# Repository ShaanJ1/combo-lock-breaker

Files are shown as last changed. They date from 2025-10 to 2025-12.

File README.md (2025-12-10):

# Combo Lock Breaker
This device can cycle through every possible combination on your lock until it finds the correct code, which is then displayed on an LCD screen. In the future this device will also be able to use Samy Kamkar's method to crack locks even faster.
### Highlights
- Fast and Accurate
- Cracks any combination lock in under ____ minutes
- LCD displays the current status, progress, and more
- Quiet & Efficient
### Showcase
*Coming soon...*
### Bill of Materials (BOM)

| **Item Name** | **URL** | **Price** | **Quantity** | **Per Package** | **Use** |
|---|---|---|---|---|---|
| Power Supply Cable | [AliExpress](https://www.aliexpress.com/item/1005007332397741.html) | $16.96 | 1 | 1 | Power |
| Nema 17 Motor | [AliExpress](https://www.aliexpress.com/item/32572890101.html?spm=a2g0o.cart.0.0.66ba38daMIFTUY&mp=1) | $23.98 | 1 | 1 | Dial turning mechanism |
| TMC2209 | [AliExpress](https://www.aliexpress.com/item/33028050145.html) | $7.49 | 1 | 3 | Motor driver |
| Analog Feedback Servo | [AliExpress](https://www.aliexpress.com/item/1005007407524023.html) | $14.81 | 1 | 1 | Shackle opening mechanism  |
| 4x4 Matrix Keypad | [AliExpress](https://www.aliexpress.com/item/1005007182495122.html?spm=a2g0o.cart.0.0.56ba38da4Y49U1&mp=1) | $2.00 | 1 | 1 | User input |
| LCD1602 I2C | [AliExpress](https://www.aliexpress.com/item/1005006151355330.html?spm=a2g0o.cart.0.0.56ba38da4Y49U1&mp=1) | $4.13 | 1 | 1 | Displays program output |
| M3 6mm Screws | [AliExpress](https://www.aliexpress.com/item/1005007264845313.html) | $2.96 | 1 | 50 | Mounting screws |
| M2.5 10mm Screws | [AliExpress](https://www.aliexpress.com/item/1005007264845313.html) | $2.96 | 1 | 50 | Mounting screws |
| M2.5 5mm Screws | [AliExpress](https://www.aliexpress.com/item/1005007264845313.html) | $2.96 | 1 | 50 | Mounting screws |
| M2 5mm Screws | [AliExpress](https://www.aliexpress.com/item/1005007264845313.html) | $2.96 | 1 | 50 | Mounting screws |
| PCBA | [JLCPCB](https://jlcpcb.com) | $73.61 | 1 | 5 PCB, 2 PCBA | Main controller |
| 1x3 PinHeader | [DigiKey](https://www.digikey.ca/en/products/detail/w%C3%BCrth-elektronik/61300311121/4846825) | $0.18 | 1 | 1 | Debug connector |
| 1x4 PinHeader | [DigiKey](https://www.digikey.ca/en/products/detail/w%C3%BCrth-elektronik/61300411121/4846827) | $0.50 | 3 | 1 | LCD & servo connectors |
| 1x8 PinHeader | [DigiKey](https://www.digikey.ca/en/products/detail/w%C3%BCrth-elektronik/61300811121/4846839) | $0.54 | 1 | 1 | Keypad connector |
| Barrel Jack | [DigiKey](https://www.digikey.ca/en/products/detail/switchcraft-inc/RAPC712BKZ/9997462) | $4.41 | 1 | 1 | Power connector |

**Total (CAD):** $165.79

**Total (USD):** $117.67

### Images
Schematic




PCB


Main Assembly



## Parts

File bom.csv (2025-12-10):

Bill of Materials
Item Name: | URL: | Price: | Quantity: | Per package | Use:
Power Supply Cable | https://www.aliexpress.com/item/1005007332397741.html | $16.96 | 1 | 1 | Power
Nema 17 Motor | https://www.aliexpress.com/item/32572890101.html?spm=a2g0o.cart.0.0.66ba38daMIFTUY&mp=1 | $23.98 | 1 | 1 | Dial turning mechanism
TMC2209 | https://www.aliexpress.com/item/33028050145.html | $7.49 | 1 | 3 | Motor Driver
Analog Feedback Servo | https://www.aliexpress.com/item/1005007407524023.html | $14.81 | 1 | 1 | Shackle opening mechanism
4x4 Matrix Keypad | https://www.aliexpress.com/item/1005007182495122.html?spm=a2g0o.cart.0.0.56ba38da4Y49U1&mp=1 | $2.00 | 1 | 1 | User input
LCD1602 I2C | https://www.aliexpress.com/item/1005006151355330.html?mp=1 | $4.13 | 1 | 1 | Displays program output
M3 6mm Screws | https://www.aliexpress.com/item/1005007264845313.html?mp=1 | $2.96 | 1 | 50 | Mounting screws
M2.5 10mm Screws | https://www.aliexpress.com/item/1005007264845313.html?mp=1 | $2.96 | 1 | 50 | Mounting screws
M2.5 5mm Screws | https://www.aliexpress.com/item/1005007264845313.html?mp=1 | $2.96 | 1 | 50 | Mounting Screws
M2 5mm Screws | https://www.aliexpress.com/item/1005007264845313.html?mp=1 | $2.96 | 1 | 50 | Mounting Screws
PCBA | https://jlcpcb.com | $73.61 | 1 | 5 PCB, 2 PCBA | Main Controller
1x3 PinHeader | https://www.digikey.ca/en/products/detail/w%C3%BCrth-elektronik/61300311121/4846825 | $0.18 | 1 | 1 | Debug Connector
1x4 PinHeader | https://www.digikey.ca/en/products/detail/w%C3%BCrth-elektronik/61300411121/4846827 | $0.50 | 3 | 1 | LCD, Motor, & Servo Connectors
1x8 PinHeader | https://www.digikey.ca/en/products/detail/w%C3%BCrth-elektronik/61300811121/4846839 | $0.54 | 1 | 1 | Keypad Connectors
Barrel Jack | https://www.digikey.ca/en/products/detail/switchcraft-inc/RAPC712BKZ/9997462 | $4.41 | 1 | 1 | Power Connector
 | Total (CAD): | $160.45
 | Total: (USD): | $114.35

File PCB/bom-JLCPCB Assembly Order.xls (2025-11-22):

JLCPCB BOM Tool - BOM Matching
BOM name：bom-JLCPCB Assembly Order.xlsx |  |  | Download Time：2025-11-21 13:03:07 |  |  |  | * Our matching results are updated in real-time, but stock and prices may change. If it's been over 24 hours, please re-match before placing your order.
PCB Assembled Qty：5 |  |  | Est. Total Price：9.0908
Your BOM |  |  |  |  | Matched Parts |  |  |  |  |  |  | Order Information
Top Designator | Bottom Designator | Comment | Footprint | JLCPCB Part # | Matches | Part # | Manufacturer | Footprint | Description | Category | Warning | JLCPCB Part # | Product link | Lib Type | Qty | Source | Total Price ($)
C1,C2 |  | 10uF | 0603 |  | Select by System | CL10A106KP8NNNC | Samsung Electro-Mechanics | 0603 | 10V 10uF X5R ±10% 0603 Multilayer Ceramic Capacitors MLCC - SMD/SMT ROHS | Multilayer Ceramic Capacitors MLCC - SMD/SMT |  | C19702 | https://jlcpcb.com/partdetail/20411-CL10A106KP8NNNC/C19702 | Basic | 4 | 4 JLCPCB | 0.0224
C4 |  | 22uF | 1206 |  | Select by System | CL31A226KAHNNNE | Samsung Electro-Mechanics | 1206 | 22uF 25V X5R ±10% 1206 Multilayer Ceramic Capacitors MLCC - SMD/SMT ROHS | Multilayer Ceramic Capacitors MLCC - SMD/SMT |  | C12891 | https://jlcpcb.com/partdetail/13537-CL31A226KAHNNNE/C12891 | Basic | 2 | 2 JLCPCB | 0.0796
C6 |  | 100nF | 0805 |  | Select by System | CC0805KRX7R9BB104 | YAGEO | 0805 | 100nF 50V X7R ±10% 0805 Multilayer Ceramic Capacitors MLCC - SMD/SMT ROHS | Multilayer Ceramic Capacitors MLCC - SMD/SMT |  | C49678 | https://jlcpcb.com/partdetail/YAGEO-CC0805KRX7R9BB104/C49678 | Basic | 2 | 2 JLCPCB | 0.0086
C7 |  | 75pF | 0402 |  | Select by System | CC0402JRNPO9BN750 | YAGEO | 0402 | 50V 75pF NP0 ±5% 0402 Multilayer Ceramic Capacitors MLCC - SMD/SMT ROHS | Multilayer Ceramic Capacitors MLCC - SMD/SMT |  | C107010 | https://jlcpcb.com/partdetail/YAGEO-CC0402JRNPO9BN750/C107010 | Extended | 20 | 20 JLCPCB | 0.022
C10,C11,C12,C13,C14,C15,C17,C20,C24,C29,C8,C9 |  | 0.1uF | 0402 |  | Select by Customer | CL05B104KO5NNNC | Samsung Electro-Mechanics | 0402 | 100nF 16V X7R ±10% 0402 Multilayer Ceramic Capacitors MLCC - SMD/SMT ROHS | Multilayer Ceramic Capacitors MLCC - SMD/SMT | 1.The comment (CL05B104KO5NNNC) of this part does not match the one (0.1uF) provided in your BOM. Please confirm; | C1525 | https://jlcpcb.com/partdetail/1877-CL05B104KO5NNNC/C1525 | Basic | 24 | 24 JLCPCB | 0.0288
C16,C3 |  | 1uF | 0402 |  | Select by System | CL05A105KA5NQNC | Samsung Electro-Mechanics | 0402 | 1uF 25V X5R ±10% 0402 Multilayer Ceramic Capacitors MLCC - SMD/SMT ROHS | Multilayer Ceramic Capacitors MLCC - SMD/SMT |  | C52923 | https://jlcpcb.com/partdetail/53938-CL05A105KA5NQNC/C52923 | Basic | 4 | 4 JLCPCB | 0.0116
C18,C19 |  | 33pF | 0402 |  | Select by System | 0402CG330J500NT | FH (Guangdong Fenghua Advanced Tech) | 0402 | 33pF 50V C0G ±5% 0402 Multilayer Ceramic Capacitors MLCC - SMD/SMT ROHS | Multilayer Ceramic Capacitors MLCC - SMD/SMT |  | C1562 | https://jlcpcb.com/partdetail/1914-0402CG330J500NT/C1562 | Basic | 4 | 4 JLCPCB | 0.004
C21 |  | 47uF | 0805 |  | Select by System | CL21A476MQYNNNE | Samsung Electro-Mechanics | 0805 | 47uF 6.3V X5R ±20% 0805 Multilayer Ceramic Capacitors MLCC - SMD/SMT ROHS | Multilayer Ceramic Capacitors MLCC - SMD/SMT |  | C16780 | https://jlcpcb.com/partdetail/17464-CL21A476MQYNNNE/C16780 | Basic | 2 | 2 JLCPCB | 0.051
C22 |  | 47uF | 1206 |  | Select by System | CL31A476MPHNNNE | Samsung Electro-Mechanics | 1206 | 10V 47uF X5R ±20% 1206 Multilayer Ceramic Capacitors MLCC - SMD/SMT ROHS | Multilayer Ceramic Capacitors MLCC - SMD/SMT |  | C96123 | https://jlcpcb.com/partdetail/97327-CL31A476MPHNNNE/C96123 | Basic | 2 | 2 JLCPCB | 0.1362
C25,C5 |  | 100uF | CP_Elec_6.3x7.7 |  | Select by Customer | RVT1V101M0607 | Honor Elec | SMD,D6.3xL7.7mm | -55℃~+105℃ 100uF 2000hrs@105℃ 35V 6.3mm 7.7mm ±20% SMD,D6.3xL7.7mm Aluminum Electrolytic Capacitors - SMD ROHS | Aluminum Electrolytic Capacitors - SMD |  | C3339 | https://jlcpcb.com/partdetail/HonorElec-RVT1V101M0607/C3339 | Extended | 6 | 6 JLCPCB | 0.2118
D1,D2,D3,D4 |  | SS34 | D_SMA |  | Select by System | SS34 | MDD(Microdiode Semiconductor) | SMA(DO-214AC) | -55℃~+125℃ 3A 40V 500uA@40V 550mV@3A Independent SMA(DO-214AC) Schottky Diodes ROHS | Schottky Diodes |  | C8678 | https://jlcpcb.com/partdetail/MDD_Microdiode_Semiconductor-SS34/C8678 | Basic | 8 | 8 JLCPCB | 0.2208
J2 |  | USB_C_Receptacle_USB2.0_14P | USB_C_Receptacle_HRO_TYPE-C-31-M-12 |  | Select by Customer | TYPE-C-31-M-12 | Korean Hroparts Elec | SMD | 1 16P 5A Female Type-C SMD USB Connectors ROHS | USB Connectors |  | C165948 | https://jlcpcb.com/partdetail/Korean_HropartsElec-TYPE_C_31_M12/C165948 | Extended | 2 | 2 JLCPCB | 0.3388
L1 |  | 4.7uH | L_7.3x7.3_H3.5 |  | Select by System | SLH0704S4R7MTT | Sunltech Tech | SMD,7.3x7.3mm | 3.5A 39mΩ 4.7uH Magnetic Shielded Inductor ±20% SMD,7.3x7.3mm Power Inductors ROHS | Power Inductors |  | C182156 | https://jlcpcb.com/partdetail/SunltechTech-SLH0704S4R7MTT/C182156 | Extended | 3 | 3 JLCPCB | 0.3732
R1,R2 |  | 5.1K | 0402 |  | Select by Customer | 0402WGF5101TCE | UNI-ROYAL(Uniroyal Elec) | 0402 | -55℃~+155℃ 5.1kΩ 50V 62.5mW Thick Film Resistor ±1% ±100ppm/℃ 0402 Chip Resistor - Surface Mount ROHS | Chip Resistor - Surface Mount | 1.The comment (0402WGF5101TCE) of this part does not match the one (5.1K) provided in your BOM. Please confirm; | C25905 | https://jlcpcb.com/partdetail/26648-0402WGF5101TCE/C25905 | Basic | 4 | 4 JLCPCB | 0.002
R3,R4 |  | 27 | 0402 |  | Select by Customer | 0402WGF270JTCE | UNI-ROYAL(Uniroyal Elec) | 0402 | -55℃~+155℃ 27Ω 50V 62.5mW Thick Film Resistor ±1% ±100ppm/℃ 0402 Chip Resistor - Surface Mount ROHS | Chip Resistor - Surface Mount | 1.The comment (0402WGF270JTCE) of this part does not match the one (27) provided in your BOM. Please confirm; | C25100 | https://jlcpcb.com/partdetail/25843-0402WGF270JTCE/C25100 | Extended | 20 | 20 JLCPCB | 0.012
R5,R7 |  | 1K | 0402 |  | Select by Customer | 0402WGF1001TCE | UNI-ROYAL(Uniroyal Elec) | 0402 | -55℃~+155℃ 1kΩ 50V 62.5mW Thick Film Resistor ±1% ±100ppm/℃ 0402 Chip Resistor - Surface Mount ROHS | Chip Resistor - Surface Mount | 1.The comment (0402WGF1001TCE) of this part does not match the one (1K) provided in your BOM. Please confirm; | C11702 | https://jlcpcb.com/partdetail/12256-0402WGF1001TCE/C11702 | Basic | 4 | 4 JLCPCB | 0.0024
R6 |  | 10K | 0402 |  | Select by Customer | 0402WGF1002TCE | UNI-ROYAL(Uniroyal Elec) | 0402 | -55℃~+155℃ 10kΩ 50V 62.5mW Thick Film Resistor ±1% ±100ppm/℃ 0402 Chip Resistor - Surface Mount ROHS | Chip Resistor - Surface Mount | 1.The comment (0402WGF1002TCE) of this part does not match the one (10K) provided in your BOM. Please confirm; | C25744 | https://jlcpcb.com/partdetail/26487-0402WGF1002TCE/C25744 | Basic | 2 | 2 JLCPCB | 0.0012
R8 |  | 100K | 0603 |  | Select by Customer | 0603WAF1003T5E | UNI-ROYAL(Uniroyal Elec) | 0603 | -55℃~+155℃ 100kΩ 100mW 75V Thick Film Resistor ±1% ±100ppm/℃ 0603 Chip Resistor - Surface Mount ROHS | Chip Resistor - Surface Mount | 1.The comment (0603WAF1003T5E) of this part does not match the one (100K) provided in your BOM. Please confirm; | C25803 | https://jlcpcb.com/partdetail/26546-0603WAF1003T5E/C25803 | Basic | 2 | 2 JLCPCB | 0.002
R9 |  | 13.7K | 0603 |  | Select by Customer | 0603WAF1372T5E | UNI-ROYAL(Uniroyal Elec) | 0603 | -55℃~+155℃ 100mW 13.7kΩ 75V Thick Film Resistor ±1% ±100ppm/℃ 0603 Chip Resistor - Surface Mount ROHS | Chip Resistor - Surface Mount | 1.The comment (0603WAF1372T5E) of this part does not match the one (13.7K) provided in your BOM. Please confirm; | C22793 | https://jlcpcb.com/partdetail/23520-0603WAF1372T5E/C22793 | Extended | 20 | 20 JLCPCB | 0.022
R21,R22 |  | 4.7K | 0402 |  | Select by Customer | 0402WGF4701TCE | UNI-ROYAL(Uniroyal Elec) | 0402 | -55℃~+155℃ 4.7kΩ 50V 62.5mW Thick Film Resistor ±1% ±100ppm/℃ 0402 Chip Resistor - Surface Mount ROHS | Chip Resistor - Surface Mount | 1.The comment (0402WGF4701TCE) of this part does not match the one (4.7K) provided in your BOM. Please confirm; | C25900 | https://jlcpcb.com/partdetail/26643-0402WGF4701TCE/C25900 | Basic | 4 | 4 JLCPCB | 0.0024
SW1 |  | SW_Push | SW_Push_SPST_NO_Alps_SKRK |  | Select by Customer | TS-1088-AR02016 | XUNPU | SMD,4x3mm | -30℃~+80℃ 1.6N 100,000 Cycles 12V 2mm 3mm 4mm 50mA Black Round Button SMD(SMT) Tab SPST Surface Mount,Vertical Without Bracket SMD,4x3mm Tactile Switches ROHS | Tactile Switches |  | C720477 | https://jlcpcb.com/partdetail/XUNPU-TS_1088AR02016/C720477 | Basic | 2 | 2 JLCPCB | 0.085
U1 |  | MCP1700x-330xxTT | SOT-23 |  | Select by Customer | MCP1700T-3302E/TT | Microchip Tech | SOT-23 | -40℃~+125℃@(Tj) 1 1.6uA 178mV@(250mA) 250mA 3.3V 44dB@(100Hz) 6V Fixed Over Temperature Protection Positive SOT-23 Voltage Regulators - Linear, Low Drop Out (LDO) Regulators ROHS | Voltage Regulators - Linear, Low Drop Out (LDO) Regulators |  | C39051 | https://jlcpcb.com/partdetail/MicrochipTech-MCP1700T_3302ETT/C39051 | Extended | 5 | 5 JLCPCB | 1.9695
U2 |  | W25Q128JVS | SOIC-8_5.3x5.3mm_P1.27mm |  | Select by Customer | W25Q128JVSIQ | Winbond Elec | SOIC-8-208mil | -40℃~+85℃ 100,000 Cycles 120ms@(32KB) 128Mbit 133MHz 1uA 2.7V~3.6V 20 Years 3ms SPI SOIC-8-208mil NOR FLASH ROHS | NOR FLASH | 1.The comment (W25Q128JVSIQ) of this part does not match the one (W25Q128JVS) provided in your BOM. Please confirm; | C97521 | https://jlcpcb.com/partdetail/WinbondElec-W25Q128JVSIQ/C97521 | Basic | 2 | 2 JLCPCB | 2.667
U3 |  | RP2040 | QFN-56-1EP_7x7mm_P0.4mm_EP3.2x3.2mm |  | Select by Customer | RP2040 | Raspberry Pi | LQFN-56(7x7) | 12bit 133MHz 30 LQFN-56(7x7) Microcontrollers (MCU/MPU/SOC) ROHS | Microcontrollers (MCU/MPU/SOC) |  | C2040 | https://jlcpcb.com/partdetail/RaspberryPi-RP2040/C2040 | Extended | 2 | 2 JLCPCB | 1.833
U6 |  | TPS54302 | SOT-23-6 |  | Select by Customer | TPS54302DDCR | Texas Instruments | TSOT-23-6 | -40℃~+125℃@(TJ) 1 3A 4.5V~28V 400kHz 45uA Adjustable Buck Buck Built-In Yes TSOT-23-6 DC-DC Converters ROHS | DC-DC Converters | 1.The comment (TPS54302DDCR) of this part does not match the one (TPS54302) provided in your BOM. Please confirm; | C311983 | https://jlcpcb.com/partdetail/TexasInstruments-TPS54302DDCR/C311983 | Extended | 5 | 5 JLCPCB | 0.8545
Y1 |  | 12MHz | Crystal_SMD_3225-4Pin_3.2x2.5mm |  | Select by Customer | X322512MSB4SI | YXC Crystal Oscillators | SMD3225-4P | -40℃~+85℃ 12MHz 20pF Crystal Oscillator ±10ppm ±20ppm SMD3225-4P Crystals ROHS | Crystals |  | C9002 | https://jlcpcb.com/partdetail/YXC_CrystalOscillators-X322512MSB4SI/C9002 | Basic | 2 | 2 JLCPCB | 0.129
J1 |  | Barrel_Jack_MountingPin | BarrelJack_GCT_DCJ200-10-A_Horizontal |  | No matches | No Part Selected
J3 |  | Conn_01x04 | PinHeader_1x04_P2.54mm_Vertical |  | No matches | No Part Selected
J4 |  | TMC2209_Module_v1.3 | TMC2209 |  | No matches | No Part Selected
J5 |  | 4x4MatrixKeypad | PinHeader_1x08_P2.54mm_Vertical |  | No matches | No Part Selected
J6 |  | Conn_01x03 | PinHeader_1x03_P2.54mm_Vertical |  | No matches | No Part Selected
J8 |  | I2C_LCD_1602 | PinHeader_1x04_P2.54mm_Vertical |  | No matches | No Part Selected
J11 |  | Analog_Feedback_Servo | PinHeader_1x04_P2.54mm_Vertical |  | No matches | No Part Selected

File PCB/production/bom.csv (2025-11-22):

Designator | Footprint | Quantity | Value | LCSC Part #
C1, C2 | 0603 | 2 | 10uF
C10, C11, C12, C13, C14, C15, C17, C20, C24, C29, C8, C9 | 0402 | 12 | 0.1uF
C16, C3 | 0402 | 2 | 1uF
C18, C19 | 0402 | 2 | 33pF
C21 | 0805 | 1 | 47uF
C22 | 1206 | 1 | 47uF
C25, C5 | CP_Elec_6.3x7.7 | 2 | 100uF
C4 | 1206 | 1 | 22uF
C6 | 0805 | 1 | 100nF
C7 | 0402 | 1 | 75pF
D1, D2, D3, D4 | D_SMA | 4 | SS34
J1 | BarrelJack_GCT_DCJ200-10-A_Horizontal | 1 | Barrel_Jack_MountingPin
J11 | PinHeader_1x04_P2.54mm_Vertical | 1 | Analog_Feedback_Servo
J2 | USB_C_Receptacle_HRO_TYPE-C-31-M-12 | 1 | USB_C_Receptacle_USB2.0_14P
J3 | PinHeader_1x04_P2.54mm_Vertical | 1 | Conn_01x04
J4 | TMC2209 | 1 | TMC2209_Module_v1.3
J5 | PinHeader_1x08_P2.54mm_Vertical | 1 | 4x4 Matrix Keypad
J6 | PinHeader_1x03_P2.54mm_Vertical | 1 | Conn_01x03
J8 | PinHeader_1x04_P2.54mm_Vertical | 1 | I2C_LCD_1602
L1 | L_7.3x7.3_H3.5 | 1 | 4.7uH
R1, R2 | 0402 | 2 | 5.1K
R21, R22 | 0402 | 2 | 4.7K
R3, R4 | 0402 | 2 | 27
R5, R7 | 0402 | 2 | 1K
R6 | 0402 | 1 | 10K
R8 | 0603 | 1 | 100K
R9 | 0603 | 1 | 13.7K
SW1 | SW_Push_SPST_NO_Alps_SKRK | 1 | SW_Push
U1 | SOT-23 | 1 | MCP1700x-330xxTT
U2 | SOIC-8_5.3x5.3mm_P1.27mm | 1 | W25Q128JVS
U3 | QFN-56-1EP_7x7mm_P0.4mm_EP3.2x3.2mm | 1 | RP2040
U6 | SOT-23-6 | 1 | TPS54302
Y1 | Crystal_SMD_3225-4Pin_3.2x2.5mm | 1 | 12 MHz

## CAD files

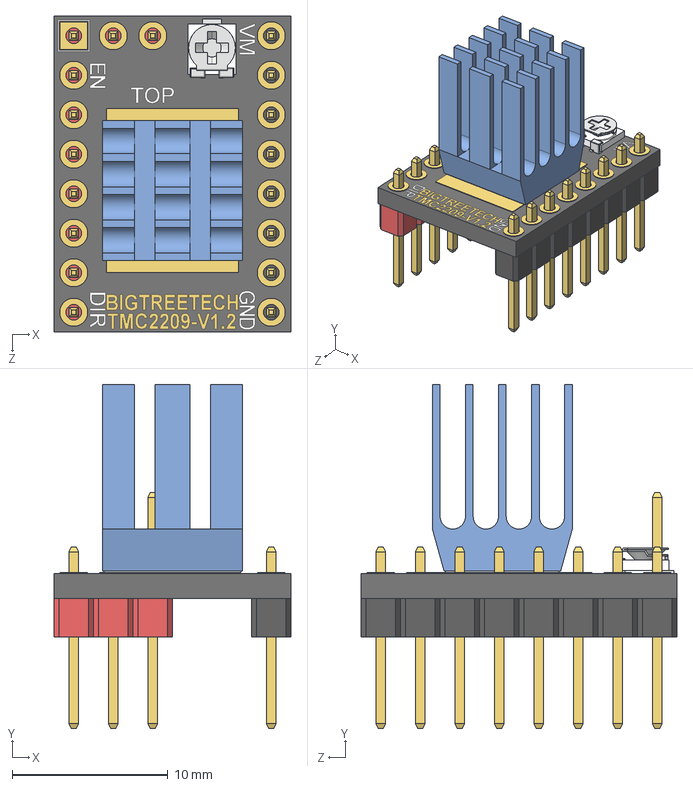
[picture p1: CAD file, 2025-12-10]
PCB/combo-lock-cracker/TMC2209.STEP
15.2 x 22.1 x 20.3 mm
TMC2209_board
Pin_Header_1x2_red
Pin_Header_1x8_red
Pin_Header_1x8_black
EVM-3E___ _________
TMC2209_heatsink

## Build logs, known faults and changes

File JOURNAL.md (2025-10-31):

<!--
  ===================    !!READ THIS NOTICE!!   ====================
  DO NOT edit this file manually. Your changes WILL BE OVERWRITTEN!
  This journal is auto generated and updated by Hack Club Blueprint.
  To edit this file, please edit your journal entries on Blueprint.
  ==================================================================
-->

## 10/7/2025 3 PM - Part Planning & Research  

Spent a few hours researching what parts I mainly need and what goes together.

- Arduino Nano (Main control module)
- Double Shaft Stepper Motor (Turns the dial, dual shaft so I can mount an encoder at the back)
- Optical Rotary Encoder (Allows for even more precise control, and accounts for missed steps, etc)
- Stepper Motor Driver (Module controlling the stepper motor)
- Voltage Regulator (Regulates the 5v to the analog feedback servo)
- Analog Feedback Servo (Opens the shaft)
- LCD Display (Shows you the interface)
- Matrix Keypad (Lets you interact with the interface)

I also would like to see if making my own pcb for this project is possible, I'll do some more research.

Next I'll need to find cheap but good parts, add any missing things needed, and calculate the total price, then I will move onto designing the project.

  

## 10/7/2025 9 PM - Rough idea on things  

- For my parts, I decided to switch out the voltage regulator for a buck converter. I did this because a buck converter has better efficiency and is better at heat management.
- I'm also switching out the arduino nano for a arduino mega since the nano doesn't have enough pins for the amount of wires I need to hook up to it, and the extra specs that the mega would give me would prevent any low memory issues I could run into in the future.

- Added Ceramic and Electrolytic capacitors
- Added Fuses

Here's a CirkitDesigner diagram I'm working on for now. (The design isn't complete yet and isn't 100% accurate). Next, I'm going to learn KiCad for schematic and PCB Designs



## 10/8/2025 3 PM - Part Updates + Installed KiCad  

- Finished the BOM for now (not including PCB or 3D printing costs yet)
- I replaced the stepper motor, encoder, and driver with an enclosed system I found on StepperOnline.ca. This not only simplified half the project for me, it was a couple bucks cheaper than my old parts too.
- Since I need more power for my new stepper motor, I will be using a 24V wall adapter with DC pigtails: female to project, male to Arduino.
- I'm also going to use 2 buck/step-down converters now, one will supply 7–12V to the Arduino's DC port, and the other will supply 5V to the other parts.
- I'm using a separate step down converter for the servo to handle voltage and current spikes when it hits the lock's shackle, which is also why I can't power it using the arduinos 5V pin as it has a chance to damage the board.

For now I'll be following some tutorials on KiCad. Once I'm comfortable, I will start to make the designs for my project.

```
[24V Wall Adapter] ---------> [Stepper Driver] > [Stepper Motor + Encoder]
                            |
                            ---------> [Step-Down 9V] -> [Arduino Mega]
                                                            |
                                                            [5V Pin] --> [LCD Display]

[24V Wall Adapter] -----> [Step-Down 5V]
                                |
                                --> [Analog Feedback Servo]
```

  

## 10/8/2025 8 PM - Future Plans  

This project is going to take way longer than I thought it would. Probably because this is my first hardware project and I have zero clue what I'm doing.

Anyways, since I'm getting tired of KiCad tutorials, I'll start working on my readme file instead. I need to do more research about my parts so I can find where I should put the capacitors and fuses, if I even need them in some areas.

An issue I currently have is that I need a multimeter to properly adjust the potentiometers on my XL4015 step down converters, which I don't have. I'll probably borrow one when needed.




## 10/8/2025 9 PM - Other considerations  

I know I'm going to get a ton of power and speed from my Nema 17 motor, but I have a new concern about if my servo is going to slow down my setup. Considering the servo will have to move very fast, and that it will have to attempt to open the shackle a few hundred or even thousands of times before stopping, I'm also concerned about the durability of the servo, I don't know if it can take that many hits.

I also really need a better name for this device, "Combination Lock Breaker" doesn't really cut it.

Here's a quick recap of what I did for the past hour
- Created readme file
- Looked at other designs of combination lock breakers, and demos
- Drafted new ideas for the future (adding a progress bar, status, etc to the display and creating more input options with the keypad)

Image taken from this [video](https://www.youtube.com/watch?v=tteG2hQaDeg)
  

## 10/9/2025 - Created a 3D lock model  

I created my combination lock model in Fusion 360. I found the dimensions of my specific lock online, but there were some missing measurements like for the dial and width of the lock so I had to measure the parts with a ruler. I'm not gonna make it super polished and good looking just yet, I just want the base idea of how everything will pan out.

I could've finished this model in less than an hour, but my Fusion kept crashing for some reason which slowed me down.



## 10/10/2025 - Creating mounts  

My current plan is to create mounts for each similar part (Keypad + LCD, Motor + Lock, etc), then I'll group them all together into one final design. I'm not that experienced in 3D modelling, so theres probably a better way to do this.



The past hour or so I've been downloading all the 3D models of the parts that I'm going to use in my project, organising my project directory, and making the LCD mount. Now I'm in the process of adding the keypad.


Still haven't really figured out the screws in Fusion yet

I want my final design to allow for the lock to be easily swappable, keep the entire thing compact, while still being able to see the action. Similar to something like this


## 10/11/2025 - Day 5  

### New ideas of how my project is going to function
For my servo, I will need to program it in a way that helps prevent excess damage by hitting the shackle full force every time. Cutting power as soon as it detects the servo hits a lot of resistance, and adding a capacitor to the servo are some ideas I have right now.


The design also needs good cooling, especially for the buck converters, so I need some additional heatsinks for that too.

#### Currently working on/plan for the day
- Schematic for the project
- Creating footprints and symbols for the parts
- Making the coupler for the motor and for the dial
- The part that will hold the lock securely in place



## 10/12/2025 10 AM - Change of plans  

Instead of having an arduino mega + pcb setup, I'm going to go ahead and make my own devboard to both reduce space and to simplify wiring. My top 2 options are currently the RP2040 and the ESP32.

After some consideration, I went ahead and chose the RP2040 module for this project over the ESP32. I liked the ESP32's chip for its wifi capabilities but ultimately chose the RP2040 because it consumes less power and has better overall hardware control. Since I also already have an LCD and Matrix keypad for my project, running a web server would've just been unnecessary overhead.



## 10/12/2025 3 PM - Created the coupler  

Finished created the coupler for my motor & lock. I made teeth on the inside for the dial by measuring out the teeth on my lock as precisely as I could with my ruler since I don't have an electric caliper. The coupler's teeth should be aligned directly with the teeth on the dial so there's minimal slipping and to ensure a good fit.


## 10/13/2025 2 PM - Created the power schematic  

Along with creating a new devboard, I dropped the XL4015 buck converter idea and went ahead with the XL1509 and the MCP1700 modules for my setup to save more space.

The board is going to have 2 sources of power, a USB-C Receptacle, and a Barrel Jack. The USB-C would mainly be used for programming the board but it can also be used to power all the components besides the stepper motor setup. The barrel jack will be the main source of the power for this board, as it provides the 24V necessary for everything to work.

The way I'm going to setup my schematic is with multiple sheets, "Power", "RP2040", and "Peripherals". I decided this would be a good way to keep everything organized and have things easily findable.



## 10/13/2025 5 PM - Finished the main RP2040 schematic sheet  

After reading a bit of the Hardware Design with the RP2040 and following some parts of Kai Pereira's guide on creating a devboard I was creating and finishing up on my schematic for the microcontroller. Everything was going good until my PC decided to randomly crash and have me lose most of my progress. The recovery file thing that KiCad has didn't work so I had to redo half of my work again which slowed me down a bit.

Nevertheless I finished the schematic and now all thats left is to create the schematic for all my peripherals then I'll be able to move onto my PCB designing.


## 10/13/2025 11 PM - Finished Schematics  

I finally finished my third and last schematic sheet. I fixed some small issues with my other sheets and organizing my sheets with textboxes and some labels. Now I'm going to get them reviewed before I go ahead and start designing the PCB.
The hardest part of this process so far was finding available parts on JLCPCB that would work for my board. I spent a little over an hour on reading datasheets and researching.

In the end I'm also going to try using some simulation software like Ansys to do some final tests on my board before finalizing and ordering my PCB to make sure everything will work as intended once I get all the parts.

For now I'll be watching some more Fusion and PCB design tutorials. Soon I'll start creating the code for my project.





## 10/14/2025 - Schematic revisions #1  

I got some advice on my schematic now I got some things to improve on. I implemented a few so far.

One thing I changed so far is removing the motor and encoder symbols entirely, since they are not apart of the pcb they don't need to be in the schematic.


With that I also replaced the stepper driver with terminal block connectors, since the driver isn't going to be directly attached to the board but will still be connected with wires.

I also read the datasheet for my logic level shifter and realized I was missing the 10k resistors on the unused pins, so I added that too.


My last change of today was changing all the global labels to hierarchial labels for better schematic practices.

Old:

New:


## 10/15/2025 12 PM - Set up VSCode  

I downloaded the Raspberry Pi Pico vscode extension and initialized my project in C. For now, I'm just going to create some very basic code with library imports and the rest will be comments of what things should be doing and how it would be structured since I don't have my project yet.



## 10/15/2025 3 PM - Finished Schematic  

Okay after some more reviews and revisions I am 99% sure my schematic is fully finished now. Now I want a little break from KiCad so I'm going to finish up writing the code and then start PCB designing.

Schematic updates:
- Added mounting holes
- Added PWR_FLAGS to GND and +24v, VBUS, +5V, and +5V Servo
- Fixed random pin layouts and properly grouped them together on the connecters
- Changed the Analog Feedback servo, I2C LCD, and the Matrix Keypad symbols to connectors since they are going to be connected with wires instead of directly being on the board.
- Fixed the barrel jack's reverse polarity protection. Before: 
After: 

## 10/16/2025 12 AM - Schematic revisions #2  

Just kidding, turns out I have more things to fix.
- I got rid of the second buck converter that was used purely for the servo since it wasn't needed, instead added a flyback diode to the servo to protect the circuit from dropping voltage when stalling.
- Changed out the XL1509 chip for its higher switching frequency(lower ripple) and similar efficiency




Everything else looks fine so far, and I finally finished assigning all the footprints after a ton of finding JLCPCB replacements and researching. Now I'll go back to writing the boilerplate code  

## 10/16/2025 11 AM - Started the PCB  

Going ahead with the PCB designing now. Haven't figured out an idea of how the board should look in the end, so for now I'm just grouping the parts on the board. I guess this is a good time to look back on the devboard tutorial and see how Kai did his in the devboard tutorial.


## 10/16/2025 3 PM - Design Updates  

When I was setting up the PCB I realized that I had two of the same connectors for each peripheral. I removed both the 1x20 pin headers since they were just duplicates and I didn't plan on needing the extra IO pins anyways.

Also I realized that my capacitors for my RP2040 were powered by 5v instead of 3v3, so I had to change that too


Now I need to make my board smaller and make a few more adjustments before I start routing.


## 10/17/2025 4 PM - Got some routing done on the PCB  

Routed most of the PCB, all thats left now is routing the connectors. I also changed the old footprint of the inductor for my 24v/5v buck converter, since I built the one one wrong and it was missing a pad, heres the new footprint



I also need to get my stepper driver connector's wiring looked at since I'm pretty sure it's wrong. 


## 10/17/2025 9 PM - Schematic Revisions #3  

Turns out the module I was using as a logic level shifter is not open collector, which is what the motor driver's datasheet recommends, so now I need to find an alternative.

I looked into the SN7407 and the 74LS07 and favoured the ladder since it already have a symbol in KiCad ready, which the other did not.

Eventually I just ended up with using transistors + resistors for the space and cost savings it provides for basically the same thing.

Since the datasheet for my driver is pretty bad it took some time to understand it all. I tied my positives to +5V and used the negatives as signals.




## 10/17/2025 10 PM - Changed the transistors  

Since the transistor was bigger than I thought, I moved to a SMD equivalent of it. I got the gist of routing and now I need to make my pcb way smaller too. Since the terminal blocks are taking up a huge chunk of my space I need to split them up across the board instead of having them all in one line.

Old transistor(left) vs new transistor(right)


Also added some placeholder functions in the code:


## 10/18/2025 11 AM - Finding viable terminal blocks  

Okay I think I'm actually done schematic-side now. 

Right now the biggest issue that im facing is finding a viable terminal block connector since I just used random footprints last time. The connector should have a footprint (or enough details on the datasheet to accurately make one), and is available at JLCPCB. I gone through like 20 so far and none of them fit my needs so far.  

## 10/18/2025 12 PM - Ready to start PCB (again)  

I finally found some parts on JLCPCB which also had a footprint(a Phoenix terminal block footprint with the same dimensions) on KiCad, now I'm going to redo my entire pcb to make it way smaller than before.





My only challenge now is figuring out how to lay out the parts without making my pcb too crammed and ugly looking.  

## 10/19/2025 - Small update  

Busy with work so I can't put as much time as I'd like to on my project, but heres some things I did.

Changes:
- Switched the flash memory for a smaller version (W25Q128JVS -> W25Q16JVZPIQ TR)


- Routed some of the PCB 
- Changed mounting holes from M3 -> M2

After finishing up the board again I will try and make it as small as possible with interfering with anything.  

## 10/21/2025 7 PM - Routed the PCB  

Here is the semi-final version of my PCB. All I need to adjust now are all the fabrication and silkscreen labels, then I need to see if I'm able to make the board smaller. 

I also filleted the edges and moved around some components to make sure everything fit in the board.



Oh yeah, the DRC is pretty mad so I gotta take care of that too.




## 10/21/2025 10 PM - Finished PCB  

I finally got rid of all the DRC errors 🥳


I tried my best to organize and fit all the silkscreen labels, but because there's a very compact area between the chip and power I couldn't keep all of them and ended up removing the ones that wouldn't fit.





Now it's time to get some reviews on the PCB

## 10/22/2025 - Fixing some PCB stuff  

Since your not supposed to use vias inside pads unless they're capped (which I have to pay extra) I went ahead and fixed all those occurences.

I also changed the thickness of the 24V traces to 0.3mm since I rounded up the calculation that I got



The top of my PCB is really crammed so I'm going to go ahead and move the MCU and it's components a little further down too.  

## 10/23/2025 7 PM - Fixing PCB #2  

My old traces were very thin so I had to change all of them to 0.2mm, along with changing the minimum clearances and stuff. All of this could've been avoided if I didn't design my board using the wrong settings 🥀

I also moved the MCU down a bit for extra room.



## 10/23/2025 9 PM - aaaaaaaaaaaaaaaaa  

This stupid little trace is not connecting for some reason and I have been spending the last 30 minutes trying to figure out why. I redrew the lines next to it a million times and tried to reroute it and nothing.



Turns out it was this because of the trace on it's right popping out a little

Dont see it?








## 10/24/2025 11 AM - Waiting for review  

I've finished up on fixing all the issues and now all that's left to do is to wait and get some more reviews in

- Moved around the traces and component arrangement so that it's a bit cleaner 



## 10/24/2025 3 PM - Finished PCB  

- Routed the GPIO0 - GPIO3 traces underneath the main chip instead of over, so it doesn't interfere with the USBD lines.
- GPIO26_ADC0 also got routed through the chip for the same reason.
- Moved the 5v/3v3 converter to the left side of the USBD lines to make it more distinguishable from the other power components

Now that I'm finished the PCB, I'm going to start working on the 3D models.

  

## 10/24/2025 6 PM - Designed Keypad Holder  

Got all the measurements for the keypad and finished a rough version for the LCD + Keypad holder.



Now I'm going to create the main base. It will hold the lock, motor, driver, and servo. Then after that I'll attach the LCD and Keypad to it, add my custom PCB, then put everything together.  

## 10/24/2025 7 PM - Rough Idea on 3D model  

I got a good start on the CAD so far



Now of course this isn't the final design, but it's what I'm going to start with. I'm planning on adding the LCD and keypad to the side of it, and have the driver and PCB on the back or even at the bottom.

My main concerns are having proper clearances so components arent too tight/loose, and a way to easily swap out locks with minimal hassle/tools.  

## 10/24/2025 11 PM - Created the base structure  

I decided that I'm going to hide the driver and my PCB underneath the structure to make things look more clean, and embed the LCD and keypad onto the front of the opener.

Instead of using a regular servo horn, I switched it out with a gear + rack system so it's more stable and it'll be more accurate when detecting shackle movement.

Next steps:
- Create the gear and servo supports
- Find/Create a 3D model for the keypad
- Create the 3D model of my PCB
- Have a place where all the wires can get routed through (the driver's power & control cables will be routed separately to avoid interference)

  

## 10/25/2025 1 PM - Created lock opening mechanism  

- Made the shackle opener
- 

- Attached teeth to the rack and attached it to the servo
- 
- 

- Created the bracket to keep the rack in place (also extended the rack a bit)
- 
I'm probably going to create an indent on the walls of the rack where the rack can slide against the bracket to properly secure it.  

## 10/25/2025 3 PM - Created Servo Mount  

Finished creating the servo mount/bracket



I couldn't find a 3D model of my exact keypad online so now I have to make my own. After creating that and setting up all the wiring + screws I think this project will finally be finished.


## 10/25/2025 6 PM - Created Keypad  



Finished creating keypad and added a bracket for it + a bracket for the LCD. Most of my time was spent trying to separate my parts again because Fusion keeps grouping them together for some reason.

My current idea for changing out the locks is having a way you can pull the stepper motor back to be able to access the lock  

## 10/26/2025 - Created lock removal mechanism  

Made a sliding motor assembly with a locking pin to easily access the combination lock at all times by just removing the pin and pushing the motor back







Now that I learned more about joints and contact sets in fusion, I'm going to do the same with my servo setup so I can simulate the gears/shackle opening too.

## 10/27/2025 10 AM - Remade design  

Since I was using bad practices to make my previous design I ended up messing up my entire project's timeline and features which I couldn't fix without doing extra hours of work. I figuired it would be easier to redo the whole project (which now only took a fraction of the time since I know what I'm doing now). 

Here are some additional changes I made:

Added more support/mounting screws
Base + Servo Bracket is smaller
Remade the lock holder so there's less lock slippage and the lock can be removed easier.



## 10/27/2025 2 PM - Finished main design  

Added the base with the LCD and the Keypad. All thats left now is to create create the 3D model of my PCB and driver, then find places for them in the design



## 10/27/2025 8 PM - Added the PCB and Driver  



I put the PCB and the driver in the most logical spots I could think of and I added mounting screws and supports for both. I also created holes for the connectors to fit the wiring through.




Now I'm going to be adding more cable organizers on the inside and I should be done the 3D modelling.  

## 10/28/2025 - Finished 3D Design  

I added holes for each port to be accessed from outside the box, and I added some dividers between terminal blocks to better organize each wires in their category. 



To access the inside I made the top cover removable with screws


Lastly I also added some mounting screws to secure the lock holder and the sliding mechanism in place


Now I'm going to work on my BOM, and I'll also get my schematic checked one last time specifically for the wiring of the driver since I want to make sure I got it correct.  

## 10/30/2025 - Updated stepper wiring  



Fixed a few issues with my stepper driver wiring and updated the PCB. Everything should be all done now



I'm going to finish up the BOM on the weekend and I should be able to ship this soon

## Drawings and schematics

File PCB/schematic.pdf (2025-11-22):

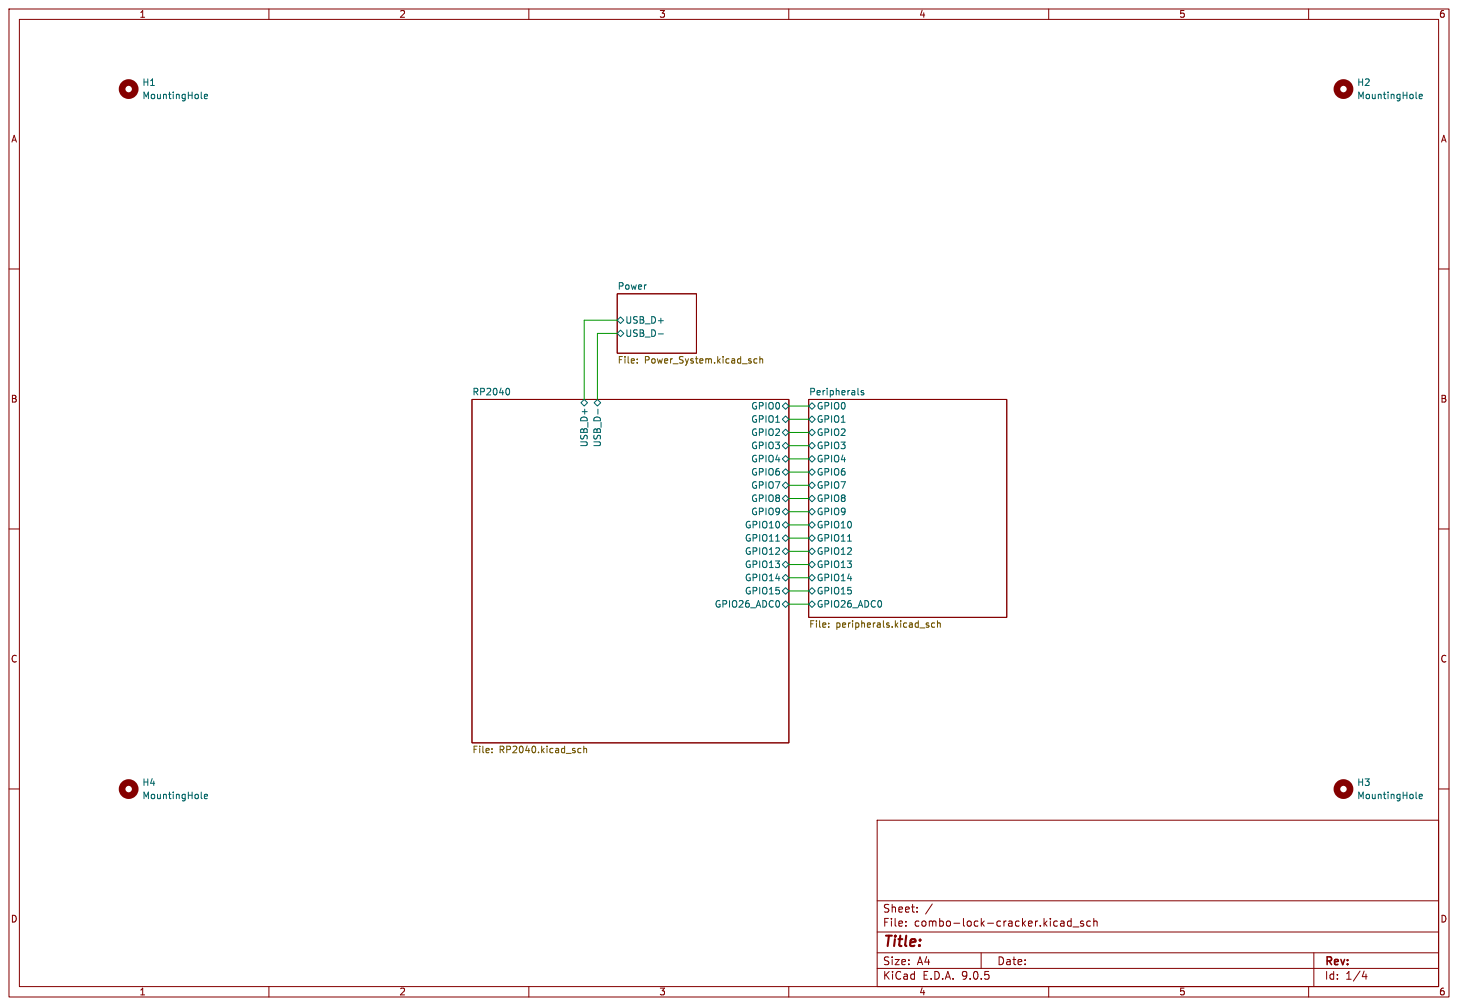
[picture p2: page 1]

Id: 1/4 Title: File: combo-lock-cracker.kicad_sch Sheet: /

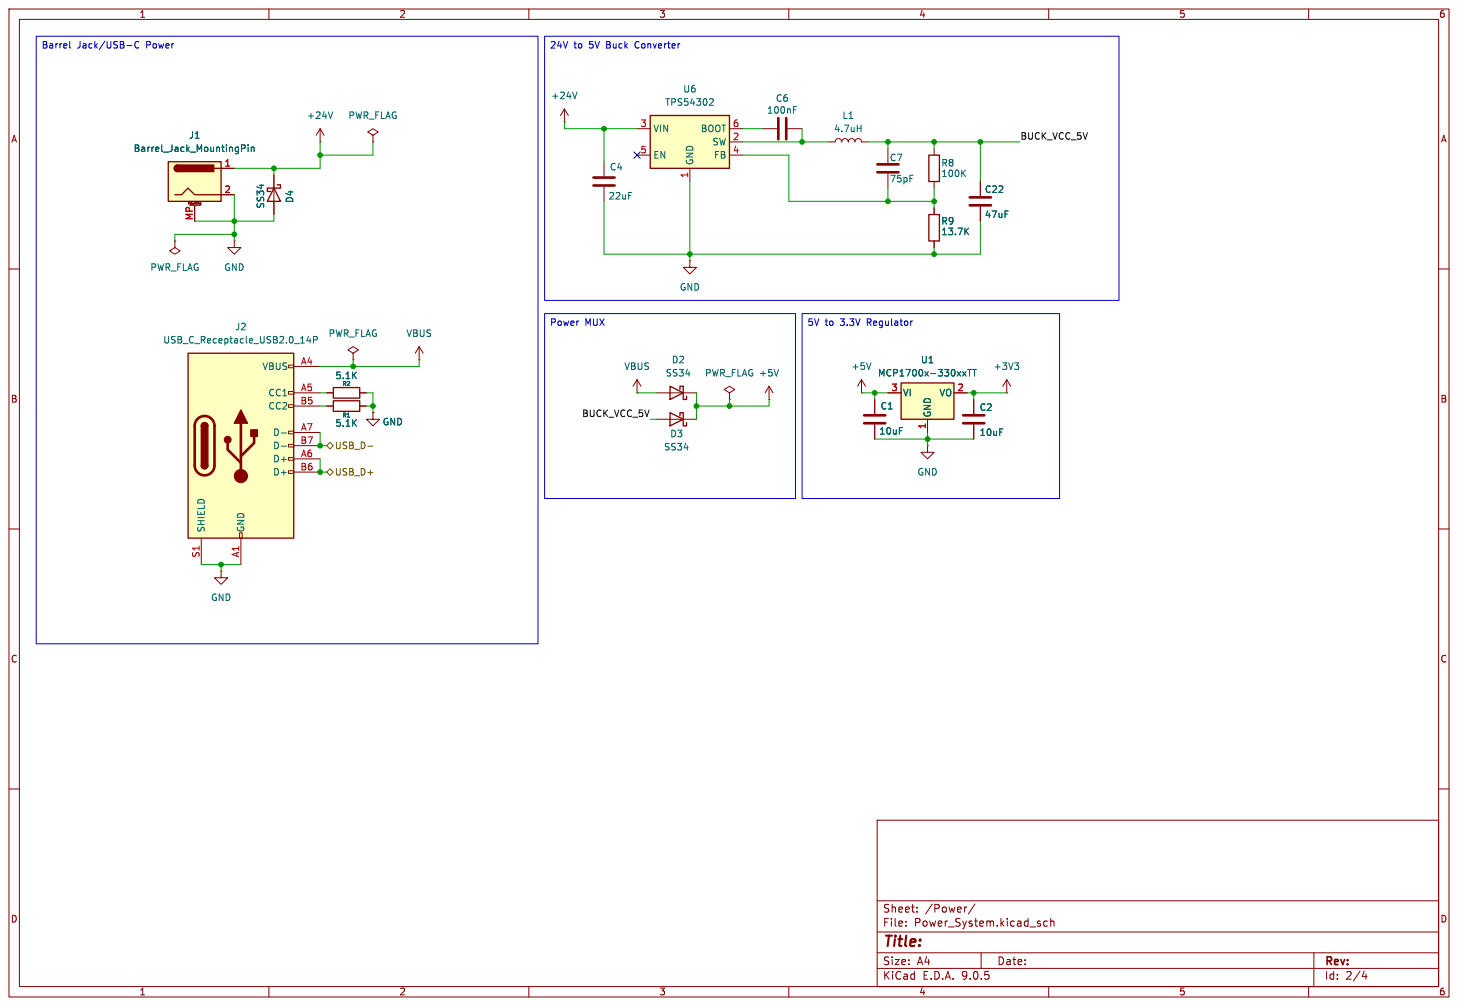
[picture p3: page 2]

1 BOOT 6 SW 2 FB 4 U6 TPS54302 SHIELD S1 GND A1 VBUS A4 CC1 A5 CC2 B5 D- A7 D- B7 D+ A6 D+ B6

Id: 2/4 Title: File: Power_System.kicad_sch Sheet: /Power/

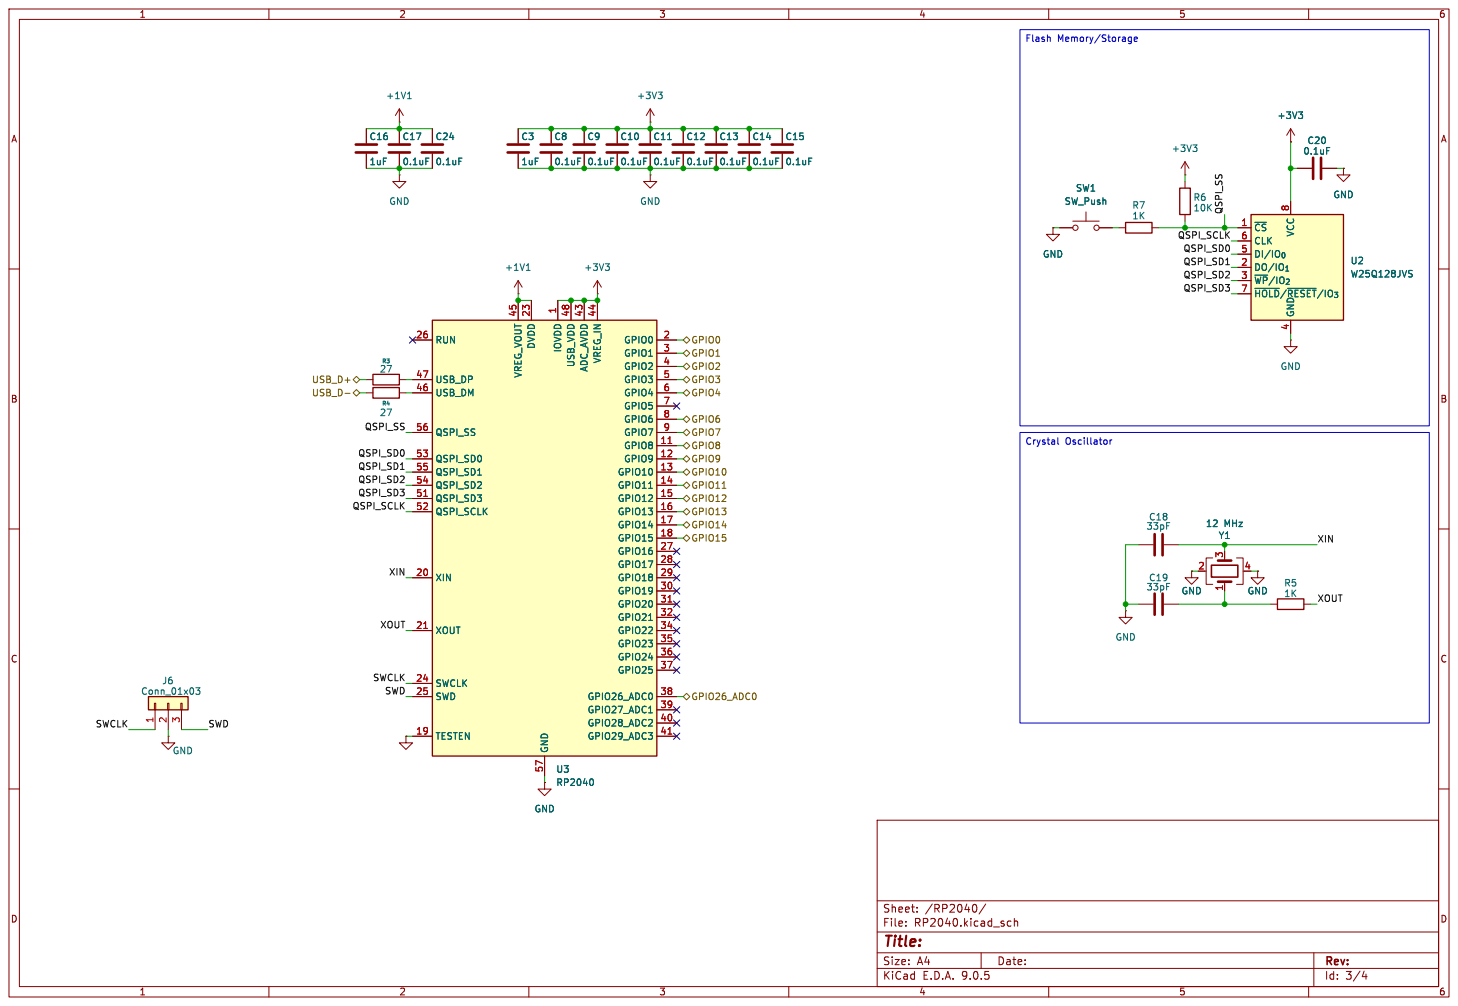
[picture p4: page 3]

Id: 3/4 Title: File: RP2040.kicad_sch Sheet: /RP2040/

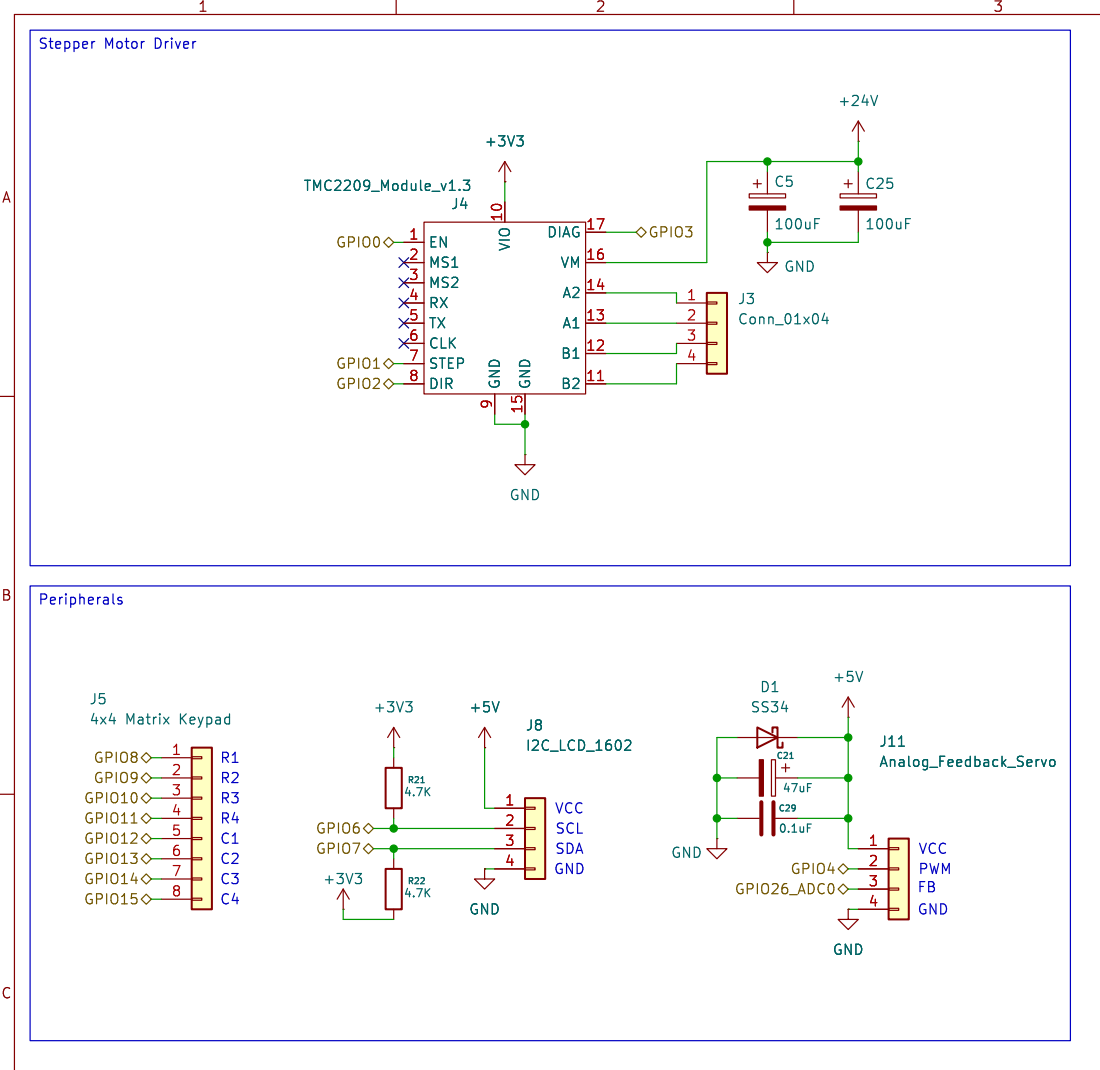
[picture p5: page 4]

9 VIO 10 GND 15 DIAG 17 VM 16 A2 14 A1 13 B1 12 B2 11

Id: 4/4 Title: File: peripherals.kicad_sch Sheet: /Peripherals/

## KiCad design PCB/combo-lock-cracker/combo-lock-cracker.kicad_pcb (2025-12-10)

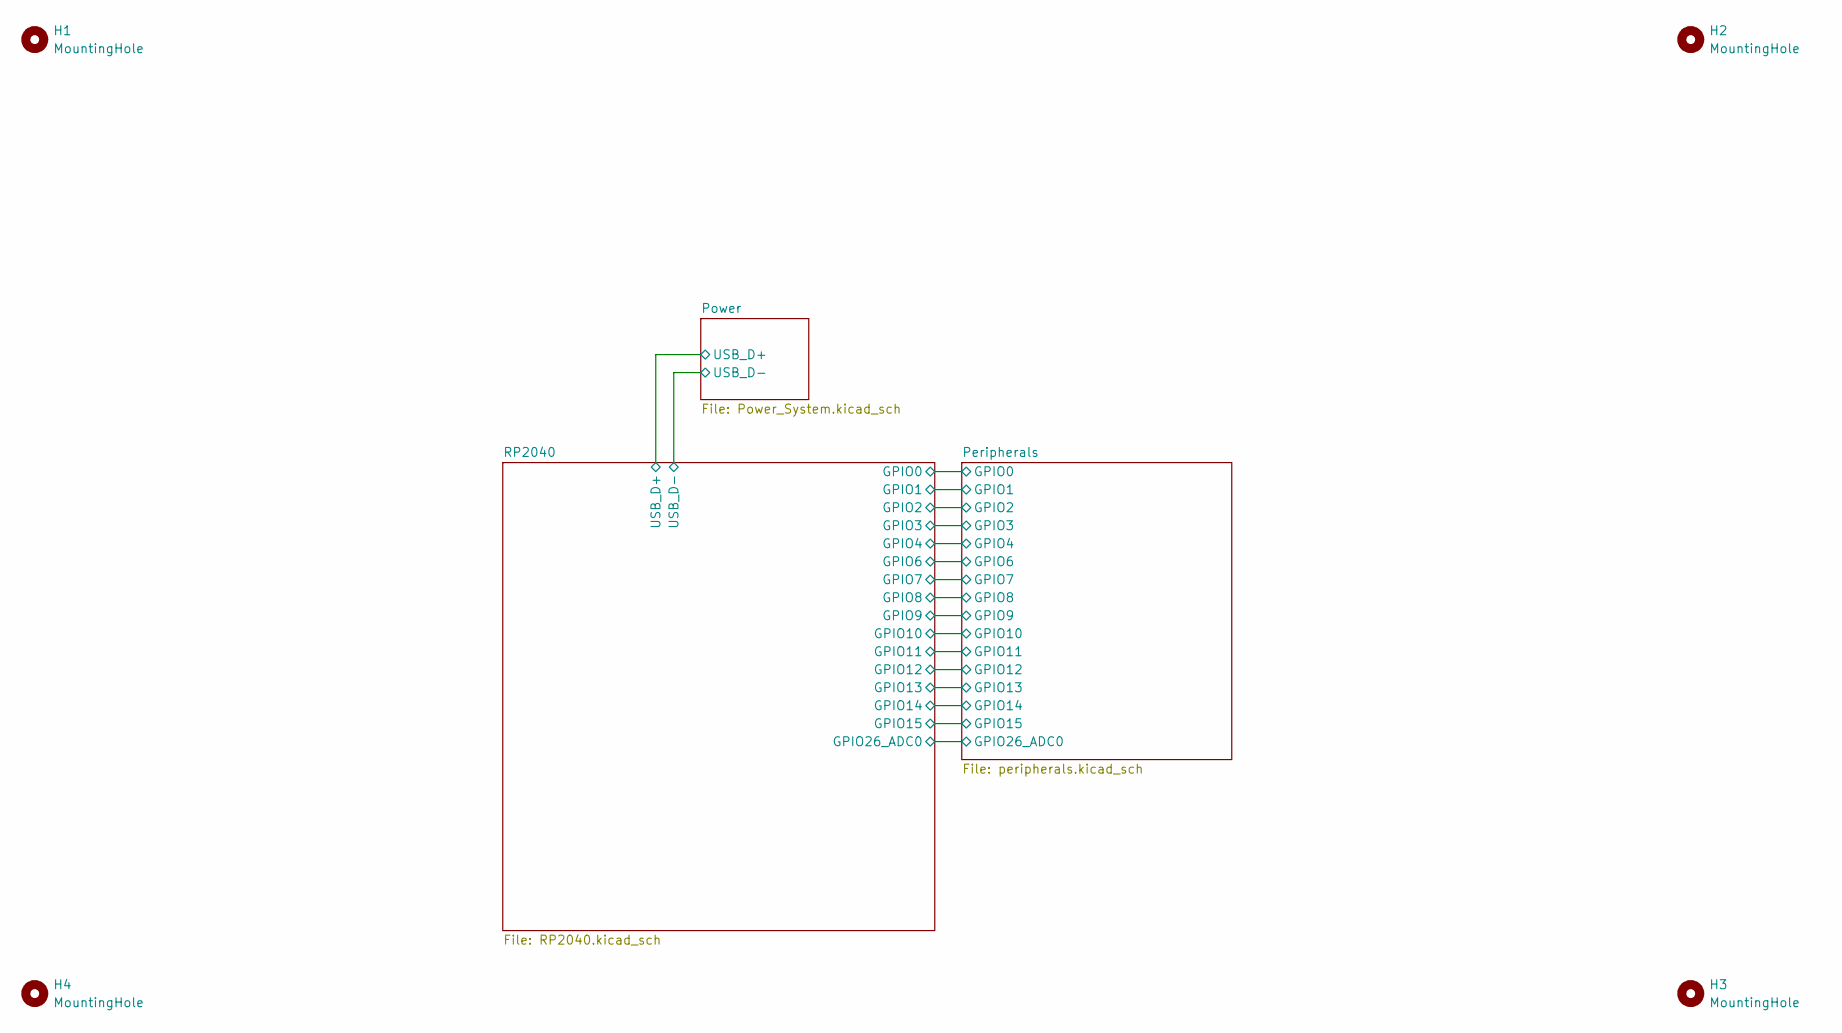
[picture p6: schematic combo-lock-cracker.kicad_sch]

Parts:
H1, H2, H3, H4: MountingHole; MountingHole_2.2mm_M2

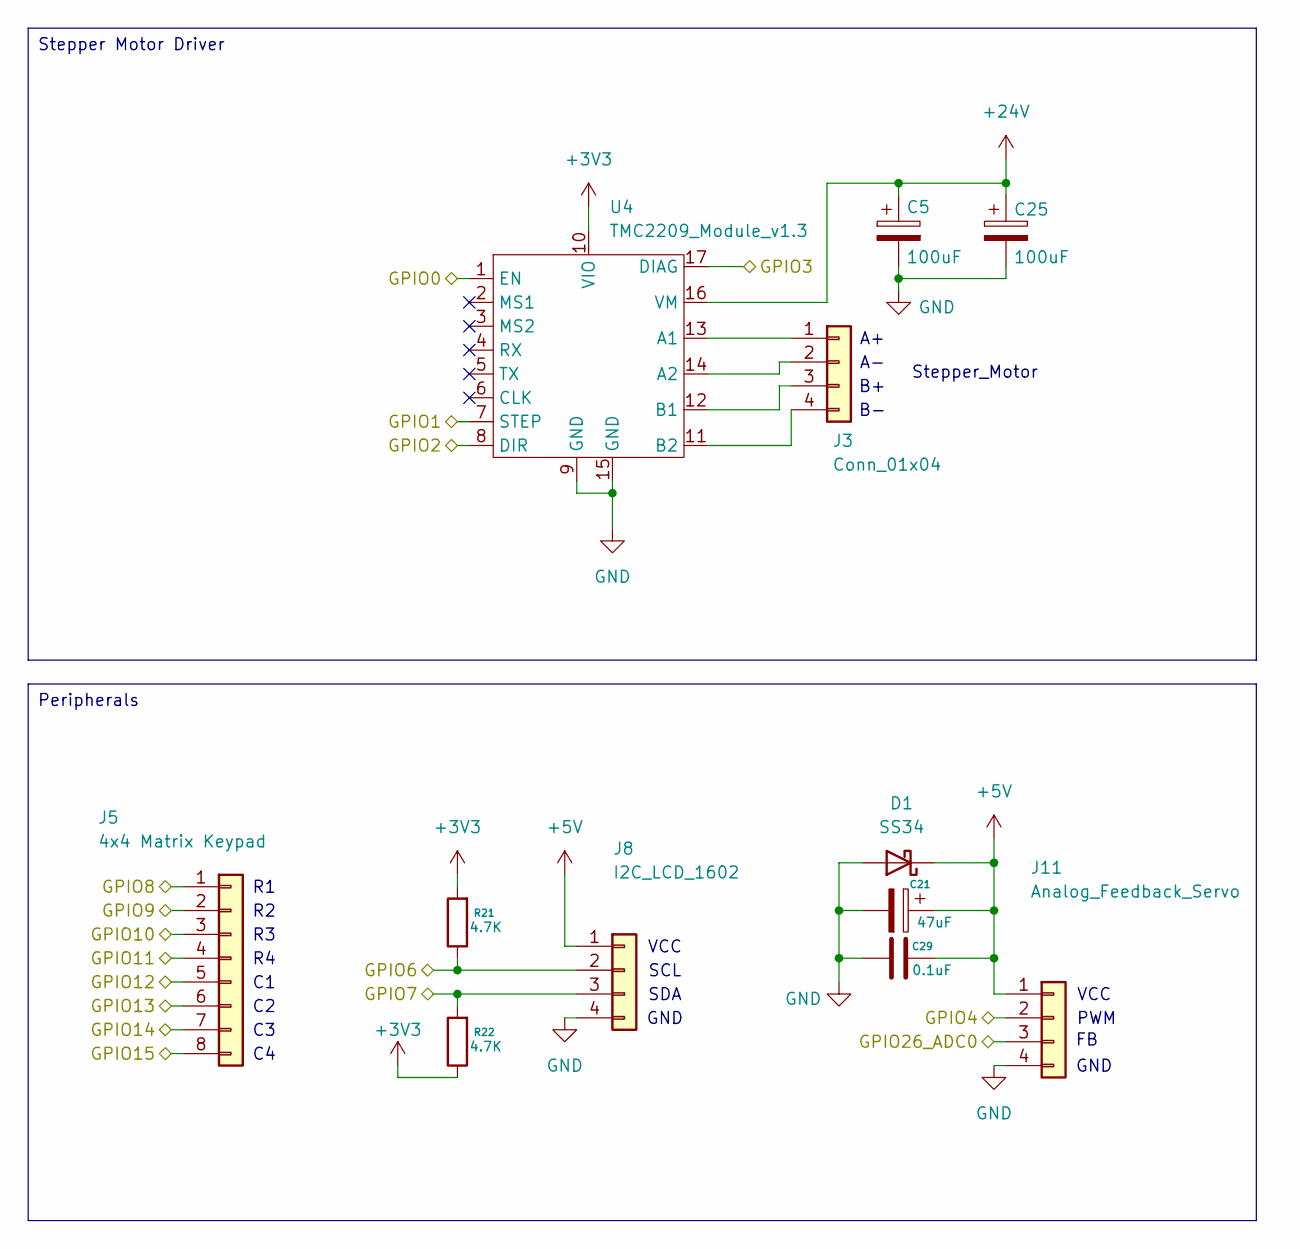
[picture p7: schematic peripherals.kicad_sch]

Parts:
C5, C25: 100uF; CP_Elec_6.3x7.7
C21: 47uF; C_0805_2012Metric
C29: 0.1uF; C_0402_1005Metric
D1: SS34; D_SMA
J3: Conn_01x04; PinHeader_1x04_P2.54mm_Vertical
J5: 4x4 Matrix Keypad; PinHeader_1x08_P2.54mm_Vertical
J8: I2C_LCD_1602; PinHeader_1x04_P2.54mm_Vertical
J11: Analog_Feedback_Servo; PinHeader_1x04_P2.54mm_Vertical
R21, R22: 4.7K; R_0402_1005Metric
U4: TMC2209_Module_v1.3; TMC2209

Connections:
+3V3: R21.2, R22.1, U4.10 (VIO); also elsewhere on the board
+5V: C21.1, C29.2, D1.1 (K), J8.1, J11.1; also elsewhere on the board
+24V: C5.1, C25.1, U4.16 (VM); also elsewhere on the board
/Peripherals/GPIO0: U4.1 (EN); also elsewhere on the board
/Peripherals/GPIO1: U4.7 (STEP); also elsewhere on the board
/Peripherals/GPIO2: U4.8 (DIR); also elsewhere on the board
/Peripherals/GPIO3: U4.17 (DIAG); also elsewhere on the board
/Peripherals/GPIO4: J11.2; also elsewhere on the board
/Peripherals/GPIO6: J8.2, R21.1; also elsewhere on the board
/Peripherals/GPIO7: J8.3, R22.2; also elsewhere on the board
/Peripherals/GPIO8: J5.1; also elsewhere on the board
/Peripherals/GPIO9: J5.2; also elsewhere on the board
/Peripherals/GPIO10: J5.3; also elsewhere on the board
/Peripherals/GPIO11: J5.4; also elsewhere on the board
/Peripherals/GPIO12: J5.5; also elsewhere on the board
/Peripherals/GPIO13: J5.6; also elsewhere on the board
/Peripherals/GPIO14: J5.7; also elsewhere on the board
/Peripherals/GPIO15: J5.8; also elsewhere on the board
/Peripherals/GPIO26_ADC0: J11.3; also elsewhere on the board
GND: C5.2, C21.2, C25.2, C29.1, D1.2 (A), J8.4, J11.4, U4.9 (GND), U4.15 (GND); also elsewhere on the board
unnamed: J3.1, U4.13 (A1)
unnamed: J3.2, U4.14 (A2)
unnamed: J3.3, U4.12 (B1)
unnamed: J3.4, U4.11 (B2)

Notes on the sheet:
VCC
SDA
GND
SCL
PWM
Stepper_Motor
Peripherals
Stepper Motor Driver

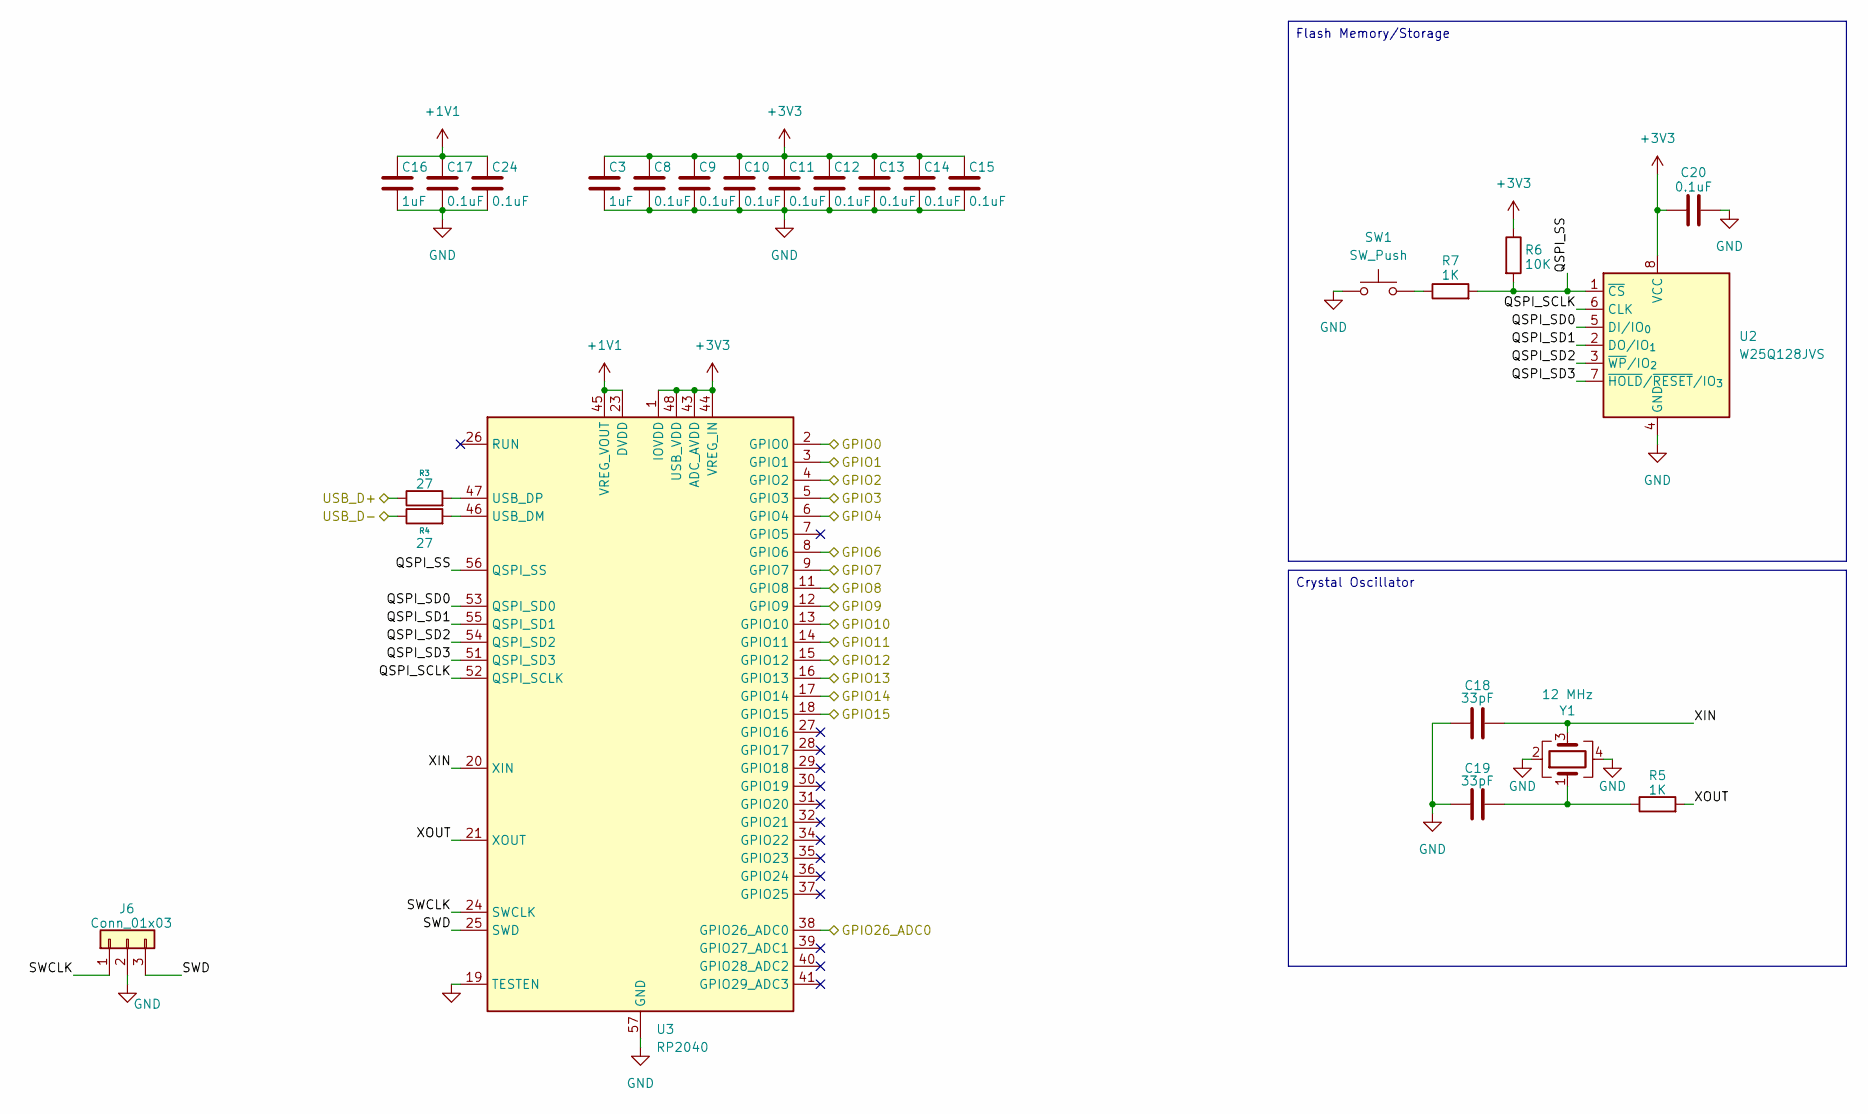
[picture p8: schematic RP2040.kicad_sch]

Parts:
C3, C16: 1uF; C_0402_1005Metric
C8, C9, C10, C11, C12, C13, C14, C15, C17, C20, C24: 0.1uF; C_0402_1005Metric
C18, C19: 33pF; C_0402_1005Metric
J6: Conn_01x03; PinHeader_1x03_P2.54mm_Vertical
R3, R4: 27; R_0402_1005Metric
R5, R7: 1K; R_0402_1005Metric
R6: 10K; R_0402_1005Metric
SW1: SW_Push; SW_Push_SPST_NO_Alps_SKRK
U2: W25Q128JVS; SOIC-8_5.3x5.3mm_P1.27mm
U3: RP2040; QFN-56-1EP_7x7mm_P0.4mm_EP3.2x3.2mm
Y1: 12 MHz; Crystal_SMD_3225-4Pin_3.2x2.5mm

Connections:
+1V1: C16.1, C17.1, C24.1, U3.23 (DVDD), U3.45 (VREG_VOUT), U3.50 (DVDD)
+3V3: C3.1, C8.1, C9.1, C10.1, C11.1, C12.1, C13.1, C14.1, C15.1, C20.1, R6.1, U2.8 (VCC), U3.1 (IOVDD), U3.10 (IOVDD), U3.22 (IOVDD), U3.33 (IOVDD), U3.42 (IOVDD), U3.43 (ADC_AVDD), U3.44 (VREG_IN), U3.48 (USB_VDD), U3.49 (IOVDD); also elsewhere on the board
/Peripherals/GPIO0: U3.2 (GPIO0); also elsewhere on the board
/Peripherals/GPIO1: U3.3 (GPIO1); also elsewhere on the board
/Peripherals/GPIO2: U3.4 (GPIO2); also elsewhere on the board
/Peripherals/GPIO3: U3.5 (GPIO3); also elsewhere on the board
/Peripherals/GPIO4: U3.6 (GPIO4); also elsewhere on the board
/Peripherals/GPIO6: U3.8 (GPIO6); also elsewhere on the board
/Peripherals/GPIO7: U3.9 (GPIO7); also elsewhere on the board
/Peripherals/GPIO8: U3.11 (GPIO8); also elsewhere on the board
/Peripherals/GPIO9: U3.12 (GPIO9); also elsewhere on the board
/Peripherals/GPIO10: U3.13 (GPIO10); also elsewhere on the board
/Peripherals/GPIO11: U3.14 (GPIO11); also elsewhere on the board
/Peripherals/GPIO12: U3.15 (GPIO12); also elsewhere on the board
/Peripherals/GPIO13: U3.16 (GPIO13); also elsewhere on the board
/Peripherals/GPIO14: U3.17 (GPIO14); also elsewhere on the board
/Peripherals/GPIO15: U3.18 (GPIO15); also elsewhere on the board
/Peripherals/GPIO26_ADC0: U3.38 (GPIO26_ADC0); also elsewhere on the board
/Power/USB_D+: R3.1; also elsewhere on the board
/Power/USB_D-: R4.1; also elsewhere on the board
/RP2040/QSPI_SCLK: U2.6 (CLK), U3.52 (QSPI_SCLK)
/RP2040/QSPI_SD0: U2.5 (DI/IO_{0}), U3.53 (QSPI_SD0)
/RP2040/QSPI_SD1: U2.2 (DO/IO_{1}), U3.55 (QSPI_SD1)
/RP2040/QSPI_SD2: U2.3 (~WP/IO_{2}), U3.54 (QSPI_SD2)
/RP2040/QSPI_SD3: U2.7 (~HOLD/~RESET/IO_{3}), U3.51 (QSPI_SD3)
/RP2040/QSPI_SS: R6.2, R7.2, U2.1 (~CS), U3.56 (QSPI_SS)
/RP2040/SWCLK: J6.1, U3.24 (SWCLK)
/RP2040/SWD: J6.3, U3.25 (SWD)
/RP2040/XIN: C18.2, U3.20 (XIN), Y1.3
/RP2040/XOUT: R5.2, U3.21 (XOUT)
GND: C3.2, C8.2, C9.2, C10.2, C11.2, C12.2, C13.2, C14.2, C15.2, C16.2, C17.2, C18.1, C19.1, C20.2, C24.2, J6.2, SW1.1, U2.4 (GND), U3.19 (TESTEN), U3.57 (GND), Y1.2, Y1.4; also elsewhere on the board
unnamed: C19.2, R5.1, Y1.1
unnamed: R7.1, SW1.2
unnamed: R4.2, U3.46 (USB_DM)
unnamed: R3.2, U3.47 (USB_DP)

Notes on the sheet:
Crystal Oscillator
Flash Memory/Storage

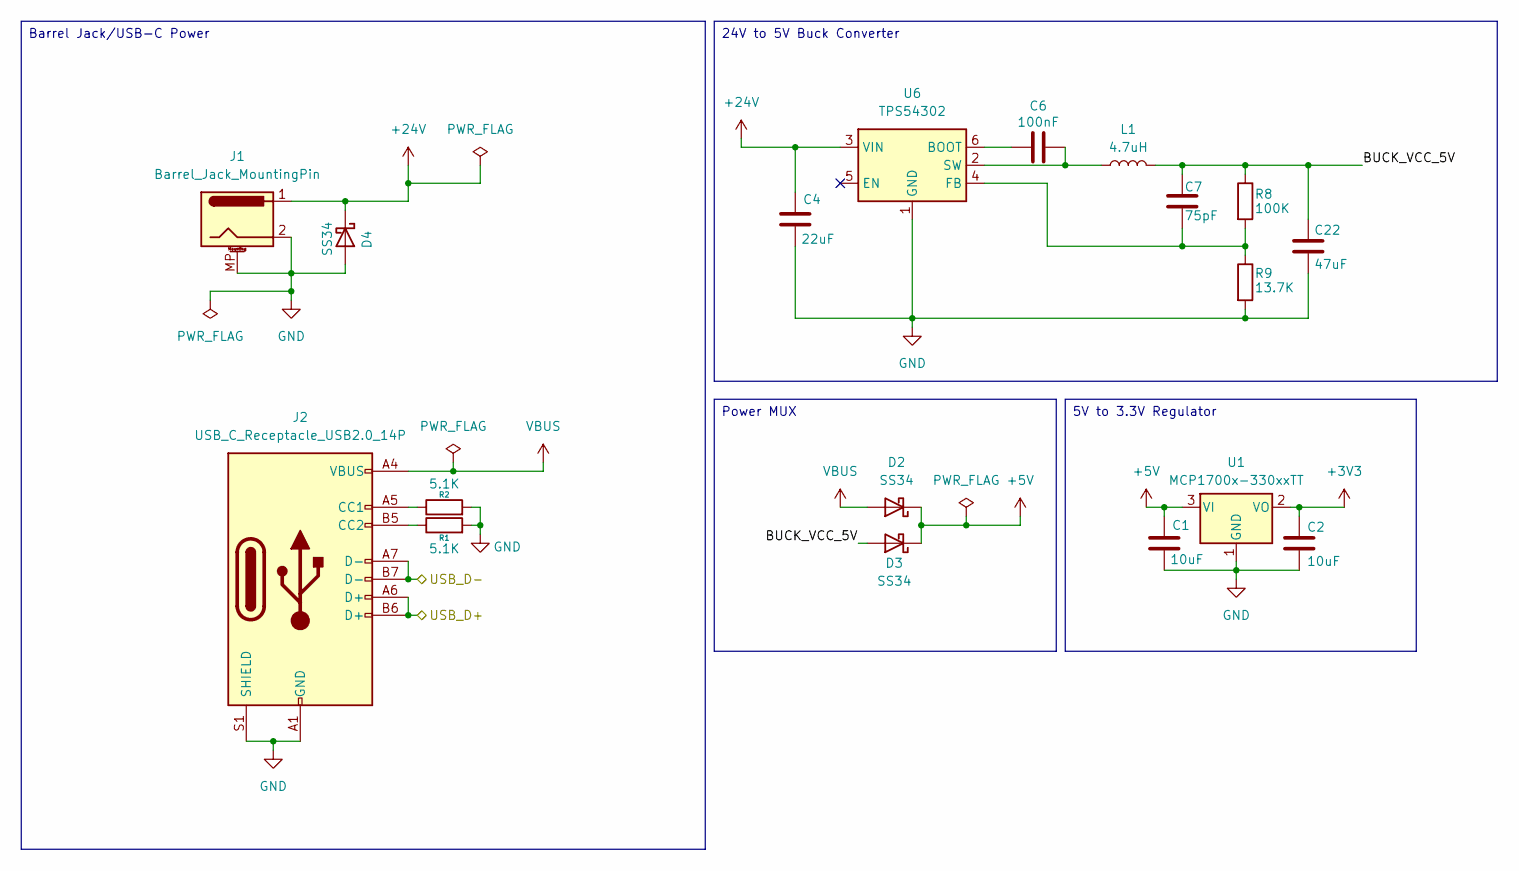
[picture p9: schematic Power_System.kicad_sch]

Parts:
C1, C2: 10uF; C_0603_1608Metric
C4: 22uF; C_1206_3216Metric
C6: 100nF; C_0805_2012Metric
C7: 75pF; C_0402_1005Metric
C22: 47uF; C_1206_3216Metric
D2, D3, D4: SS34; D_SMA
J1: Barrel_Jack_MountingPin; BarrelJack_GCT_DCJ200-10-A_Horizontal
J2: USB_C_Receptacle_USB2.0_14P; USB_C_Receptacle_HRO_TYPE-C-31-M-12
L1: 4.7uH; L_7.3x7.3_H3.5
R1, R2: 5.1K; R_0402_1005Metric
R8: 100K; R_0603_1608Metric
R9: 13.7K; R_0603_1608Metric
U1: MCP1700x-330xxTT; SOT-23
U6: TPS54302; SOT-23-6

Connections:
+3V3: C2.1, U1.2 (VO); also elsewhere on the board
+5V: C1.1, D2.1 (K), D3.1 (K), U1.3 (VI); also elsewhere on the board
+24V: C4.1, D4.1 (K), J1.1, U6.3 (VIN); also elsewhere on the board
/Power/BUCK_VCC_5V: C7.1, C22.1, D3.2 (A), L1.2, R8.1
/Power/USB_D+: J2.A6 (D+), J2.B6 (D+); also elsewhere on the board
/Power/USB_D-: J2.A7 (D-), J2.B7 (D-); also elsewhere on the board
GND: C1.2, C2.2, C4.2, C22.2, D4.2 (A), J1.2, J1.MP (MountPin), J2.A1 (GND), J2.A12 (GND), J2.B1 (GND), J2.B12 (GND), J2.S1 (SHIELD), R1.2, R2.2, R9.2, U1.1 (GND), U6.1 (GND); also elsewhere on the board
unnamed: J2.A5 (CC1), R1.1
unnamed: J2.B5 (CC2), R2.1
unnamed: C6.1, U6.6 (BOOT)
unnamed: C7.2, R8.2, R9.1, U6.4 (FB)
unnamed: C6.2, L1.1, U6.2 (SW)
VBUS: D2.2 (A), J2.A4 (VBUS), J2.A9 (VBUS), J2.B4 (VBUS), J2.B9 (VBUS)

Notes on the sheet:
24V to 5V Buck Converter
Barrel Jack/USB-C Power
5V to 3.3V Regulator
Power MUX

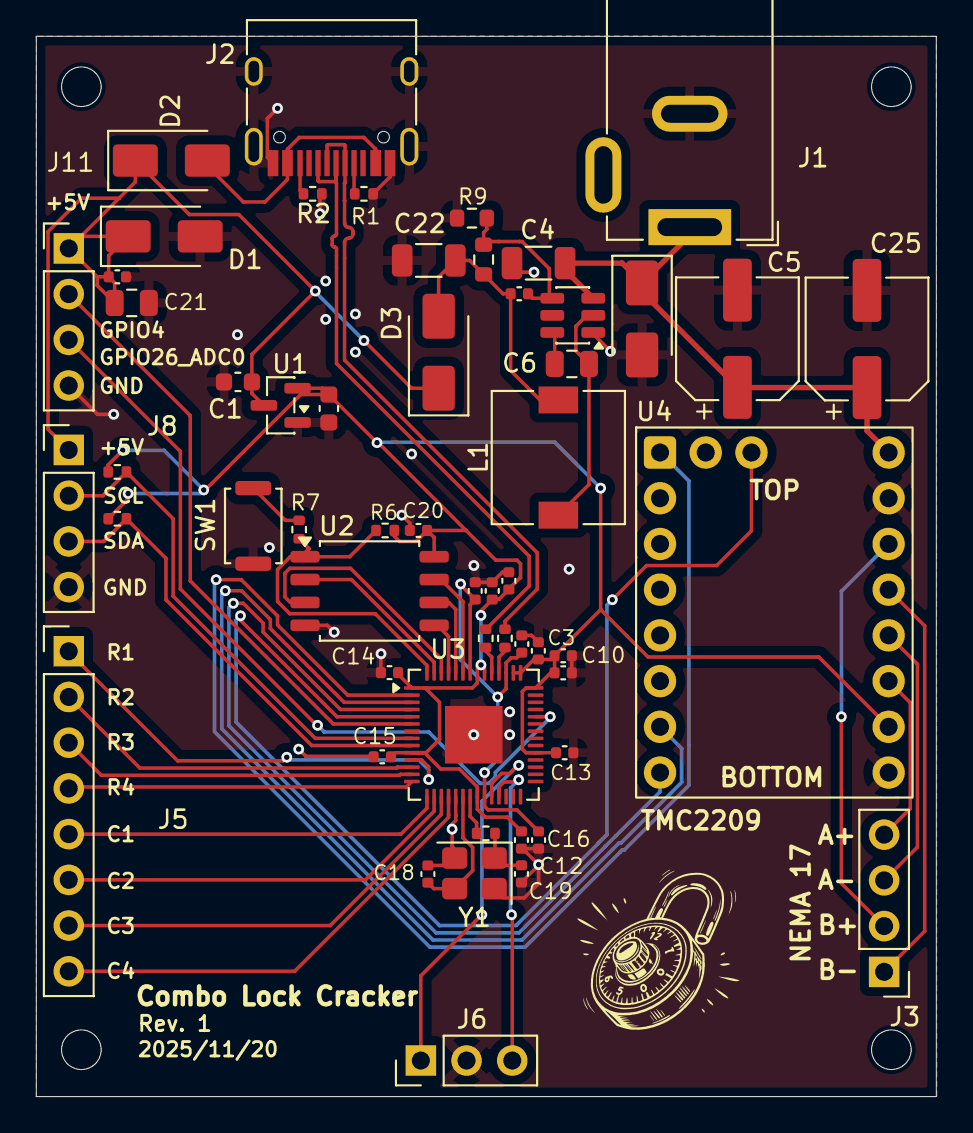
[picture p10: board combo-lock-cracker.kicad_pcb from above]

Board: 4 copper layers, 50.0 x 58.9 mm, 59 parts (0 on the bottom side), 48 nets.

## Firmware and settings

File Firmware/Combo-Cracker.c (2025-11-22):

#include <stdio.h>
#include "pico/stdlib.h"
#include "hardware/i2c.h"
#include "hardware/pwm.h"
#include "hardware/uart.h"
#include "hardware/gpio.h"

/* 
 * Hardware: I2C, LCD, Matrix Keypad, Nema 17, TMC2209
 *
 * Pins:
 * - GPIO0: PUL- Stepper Driver
 * - GPIO1: DIR- Stepper Driver
 * - GPIO2: ENA - Stepper Driver
 * - GPIO3: ALM - Stepper Driver Alarm
 * - GPIO4: PWM Analog Feedback Servo
 * - GPIO26_ADC0: FB Analog Feedback Servo 
 * - GPIO6: SCL I2C LCD 1602
 * - GPIO7: SDA I2C LCD 1602
 * - GPIO8: Row 1 Keypad
 * - GPIO9: Row 2 Keypad
 * - GPIO10: Row 3 Keypad
 * - GPIO11: Row 4 Keypad
 * - GPIO12: Column 5 Keypad
 * - GPIO13: Column 6 Keypad
 * - GPIO14: Column 7 Keypad
 * - GPIO15: Column 8 Keypad
*/

// --- Pin Defines ---
// #define STEPPER_PUL_PIN 0
// #define STEPPER_DIR_PIN = 1
// #define STEPPER_ENA_PIN = 2
// #define STEPPER_ALM_PIN = 3

// #define SERVO_PWM_PIN 5
// #define SERVO_FB_PIN 26 // ADC0

// #define LCD_SCL_PIN 6
// #define LCD_SDA_PIN 7

// #define KEYPAD_ROW1_PIN 8
// #define KEYPAD_ROW2_PIN 9
// #define KEYPAD_ROW3_PIN 10
// #define KEYPAD_ROW4_PIN 11
// #define KEYPAD_COLUMN1_PIN 12
// #define KEYPAD_COLUMN2_PIN 13
// #define KEYPAD_COLUMN3_PIN 14
// #define KEYPAD_COLUMN4_PIN 15

// ---------------------------

void initStepper() {

}

void enableDriver() {
    
}

void calibrateStepper() {

}

void set_Stepper_Direction(int dir) {
    
}

void stepper_Pulse_Blocking(int steps, int pulse_delay) { // steps, delay

}

void moveStepperToPositiion(int position) {

}

void turnStepperClockwise(int amount) {
    
}

void stepper_counterclockwise(int amount) {
    
}

void displayToLCD(const char* message) {

}

// After the combination is found, disable the motor, and when it starts back up again, enable it.
// Enabling the motor makes the shaft hold its torque
// Disabling the motor makings the shaft able to free spin by hand

// -------------IMPORTANT NOTES:---------------
//  ENA must be ahead of DIR by at least 200ms. Usually, ENA+ and ENA- are NC(not connected). See“Connector P1 Configurations” for more information. 
//  DIR must be ahead of PUL effective edge by 2us to ensure correct direction;
//  Pulse width not less than 1us;
//  Low level width not less than 1us;
//  Duty cycle of PUL signal is recommended 50%.

double timeTaken = 0;

int main() {
    // Init standard libraries
    stdio_init_all();

    // Initialize hardware pins
    
    
}

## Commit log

2025-11-10 updated BOM
    [bom.xlsx]
2025-11-17 BOM changes
    Changed to .csv format
    Found cheaper PSU & analog feedback servo on aliexpress
    Updated Barrel Jack connector to the right one (needed 24v, old one was only up to 20v)
    [bom.csv, bom.xlsx]
2025-11-22 Switched out Motor & Driver
    [bom-JLCPCB Assembly Order.xls, bom.csv, designators.csv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]
2025-12-10 actual updated pcb
    uploaded the actual pcb and fixed motor pin wiring
    [Power_System.kicad_sch, RP2040.kicad_sch, TMC2209.STEP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]
